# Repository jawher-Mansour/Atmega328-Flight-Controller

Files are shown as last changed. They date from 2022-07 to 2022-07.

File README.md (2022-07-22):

# Atmega328-Flight-Controller
A  Flight Controller board for a quadcopter based on YMFC Joop Brokking's code.

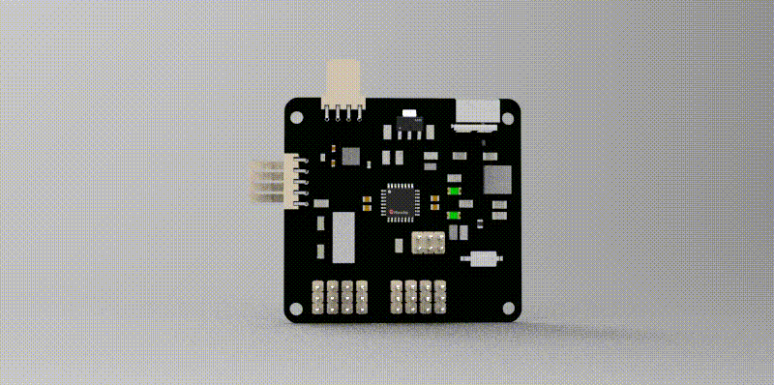
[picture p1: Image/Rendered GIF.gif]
Board Animated GIF
<h1 align="center"></h1>

This is the readme file of the Atmega328-Flight Controller project, which is my contribution to the OPEN SOURCE community. The board was developed by LAB619 Engineering & Consulting Services which is a tech company based in Tunisia that is specialized in custom machine fabrication and embedded solution development, the company is also specialized in developing IoT solutions (LoRa, GPRS, and WiFi), PCB and mechanical design. You can check the website for further information: [LAB619 Engineering & Consulting Services](https://lab619.tn)

This board is an Atmega328 MCU-based flight controller for quadcopters that is easy to build and fun to fly. The board is compatible with Joop BROKKING YMFC-AL (Your Multi-copter Flight Controller -Auto Leveling). Auto leveling means that when you release the sticks the quadcopter levels itself.

## Broadly, this repository consists of:

- Hardware designs (developed using Altium).
- PDF for Schematics
- Bill of Materials Files 
- Footprint Position File 
- Gerber Files 
- Software written using Arduino-IDE
```
📦Atmega328-Flight-Controller
 ┣ 📂Fabrication
 ┃ ┣ 📂Assembly
 ┃ ┗ 📂Gerber
 ┣ 📂Image
 ┣ 📂Altium Files
 ┣ 📂Software
 ┣ 📜.gitignore
 ┣ 📜README.md
 ┣ 📜fabrication and assembly drawings.pdf
 ┗ 📜Schematics.pdf
```
---
## Board Specifications :

The board currently includes:

- MCU: Atmega328 with an I2C, UART, and SPI interfaces.
- IMU: MPU6050 which is a 3-axis gyroscope and a 3-axis accelerometer on the same silicon die with an I2C interface and an interrupt pin.
- 4 PWM outputs to control the motors.
- 4 Timer input channels for the Inputs.
- Batterie voltage measurement system (voltage divider and Zener diode for protection).
- FTDI and ICSP interfaces for programming & debugging.
- LEDs for signaling.

<table>
  <tr>
    <td> 
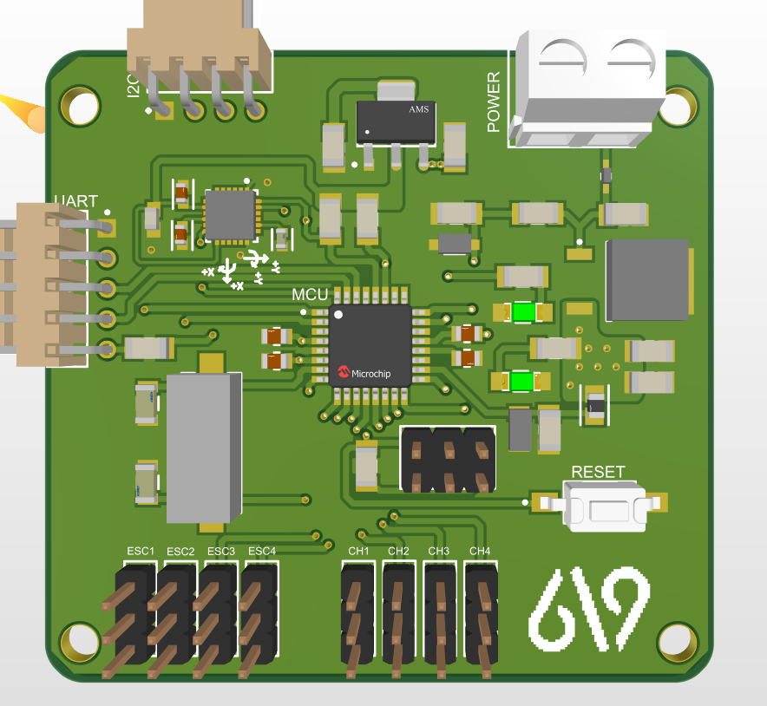
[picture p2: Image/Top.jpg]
PCB Rendred Top View
     
  </td>
  <td>   
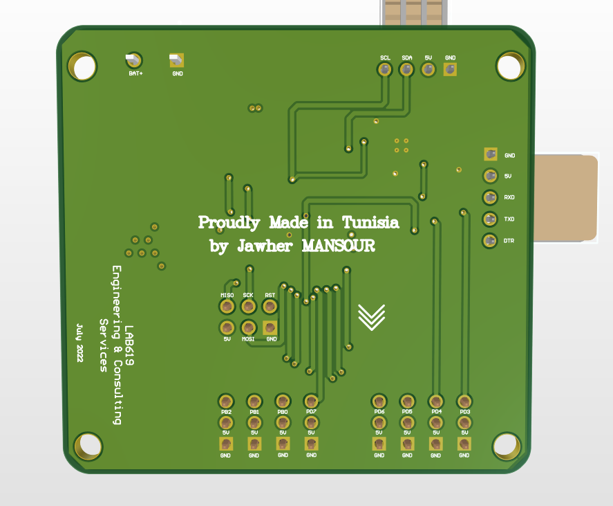
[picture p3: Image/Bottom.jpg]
PCB Rendred Bottom View
    
  </td>  
  </tr> 
  <tr>
    <td> 
      <center> Top side of the PCB </center>
  </td>
  <td> 
      <center>Bottom  side of the PCB</center>
  </td>  
  </tr> 
</table>

## Getting Started:

In order to program the board, it is necessary to use an **AVR ICSP** Programmer. 

If you don't have an AVR ICSP you can use any Arduino board as a programmer as shown in this [link](https://docs.arduino.cc/built-in-examples/arduino-isp/ArduinoISP)

---
### Fabrication

This board can be manufactured and assembled by [JLCPCB](https://jlcpcb.com/). Check the fabrication folder for files related to manufacturing the board

---
### How to setup and program the board 

Use an AVR ICSP programmer or any Arduino board as a programmer to connect to **Atmega328-Flight-Controller**

You need to connect AVR ICSP's 5V,MOSI,MISO,SCK,RESET,GND to Flight Controller board's 5V,MOSI,MISO,SCK,RESET,GND.

Further details can be found on Joop BroKking web page [link](http://www.brokking.net/ymfc-al_main.html) or you can follow this amazing video by Joop [Youtube Video](https://www.youtube.com/watch?v=DYpHB-LfloI&t=1s)

<table>
  <tr>
    <td> 
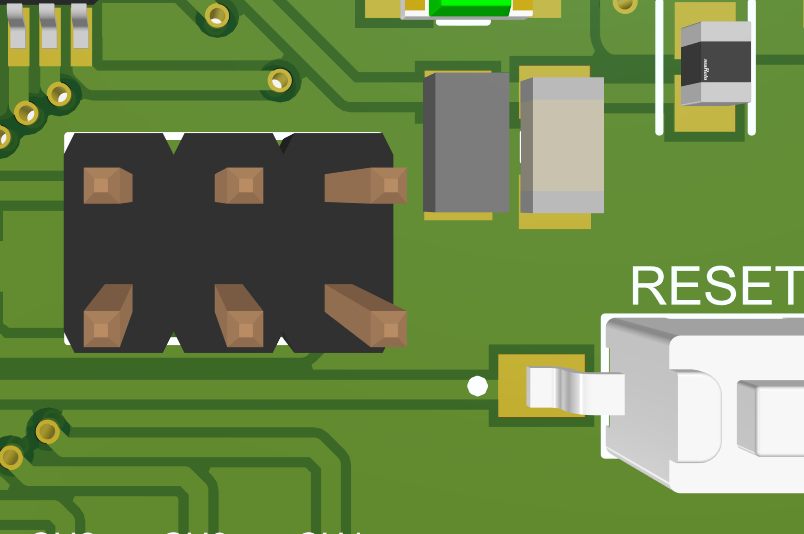
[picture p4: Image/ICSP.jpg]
     
  </td>
  <td>   
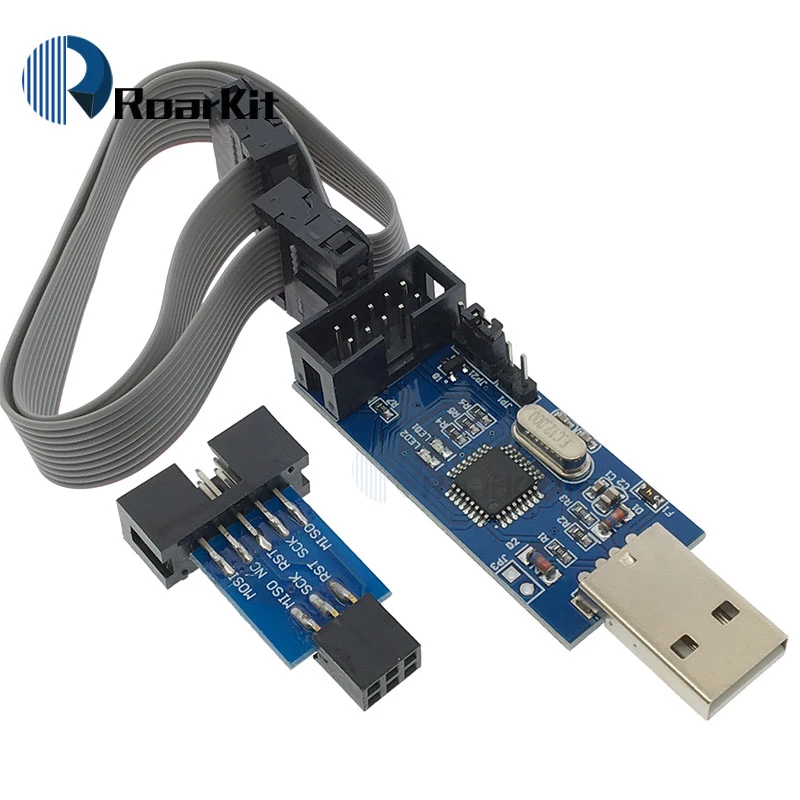
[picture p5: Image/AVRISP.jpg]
   
  </td>  
  </tr> 
  <tr>
    <td> 
    <center>Programming Pins</center>
  </td>
  <td>   
   <center>AVR ICSP programmer</center>
  </td>  
  </tr> 
</table>

---

## Useful ressources
### Datatsheets

- Atmega328 Datasheet [Atmega328](https://ww1.microchip.com/downloads/en/DeviceDoc/Atmel-7810-Automotive-Microcontrollers-ATmega328P_Datasheet.pdf)
- MPU6050 Datasheet [MPU6050](https://invensense.tdk.com/wp-content/uploads/2015/02/MPU-6000-Datasheet1.pdf)

## Credits

- PCB design and hardware engineering : Jawher MANSOUR [Web ](https://jawher-mansour.github.io/) email: jawhermansour@outlook.com

- Software design : Joop Brokking [Web](http://www.brokking.net/)

---

**Note:** ***This repository is reserved for the hardware part of this project, as well as the embedded software of the project.***

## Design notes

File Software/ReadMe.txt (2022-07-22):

Thank you for downloading the YMFC-AL software package. 

Current version: 1.4 April 30, 2017

Content:
YMFC-AL_setup.ino
YMFC-AL_esc_calibrate.ino
YMFC-AL_Flight_controller.ino

Revision update:
=====================================================================================================================================================

Version 1.4 April 30, 2017
The calibration sketch stops working when a character or number is send. When sending a character via the serial monitor of some Arduino IDE’s a line feed is also send. Because the ESC calibration program only expects one character the program stops working.

In the code the line:
data = Serial.read();                                                               //Read the incomming byte.

Is changed into:
data = Serial.read();                                                               //Read the incomming byte.
delay(100);                                                                         //Wait for any other bytes to come in
while(Serial.available() > 0)loop_counter = Serial.read();                          //Empty the Serial buffer.
=====================================================================================================================================================

Version 1.3 October 30, 2016
With the newer Arduino IDE versions (1.6.x and up) the setup program hangs due to optimization of the compiler. This is fixed in this version.

The starting speed of the motors is reduced to 1100us.

=====================================================================================================================================================

Version 1.2 - July 12, 2016
The last code did not fix the complete problem so I had to make another adjustment to the code. The acc_x and acc_y values can also be negative so a simple smaller or greater test does not work.
Therefor I changed the code to:

if(abs(acc_y) < acc_total_vector){                                        //Prevent the asin function to produce a NaN
  angle_pitch_acc = asin((float)acc_y/acc_total_vector)* 57.296;          //Calculate the pitch angle.
}
if(abs(acc_x) < acc_total_vector){                                        //Prevent the asin function to produce a NaN
  angle_roll_acc = asin((float)acc_x/acc_total_vector)* -57.296;          //Calculate the roll angle.
}

This prevents a division by zero and the input value for the asin function will always be smaller than 1.
=====================================================================================================================================================

Version 1.1 - July 11, 2016
There was a NaN (not a number) problem in the code. When flying more aggressive the quadcopter could become uncontrolable. The NaN problem is caused by the following:
When the absolute value of acc_y or acc_x becomes larger that the acc_total_vector the values provided to the asin function is larger than 1 and the asin function produces a NaN.
It recovers when the acc_total_vector becomes larger that the acc_x or acc_y values. But due to the complimentary filter the NaN error persists.
This problem will only occur when flying aggressive / fast descents. 

I changed the code as followed:
from:
angle_pitch_acc = asin((float)acc_y/acc_total_vector)* 57.296;            //Calculate the pitch angle.
angle_roll_acc = asin((float)acc_x/acc_total_vector)* -57.296;            //Calculate the roll angle.

to:
if(acc_y > acc_total_vector){
  angle_pitch_acc = asin((float)acc_y/acc_total_vector)* 57.296;            //Calculate the pitch angle.
}
if(acc_x > acc_total_vector){
  angle_roll_acc = asin((float)acc_x/acc_total_vector)* -57.296;            //Calculate the roll angle.
}
=====================================================================================================================================================

Version 1.0 - July 3, 2016
Release
=====================================================================================================================================================

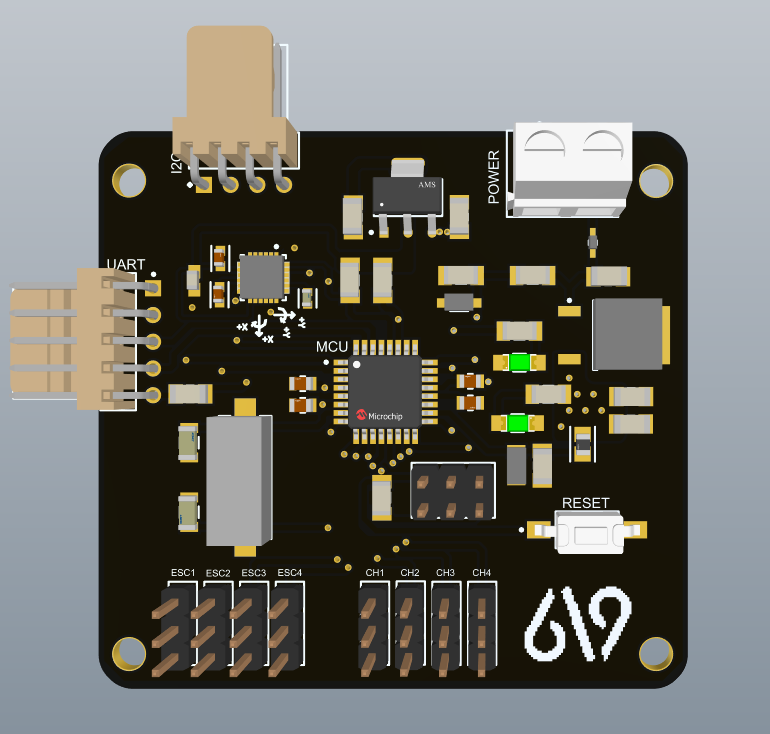
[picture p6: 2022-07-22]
Image/CapturePCB.jpg

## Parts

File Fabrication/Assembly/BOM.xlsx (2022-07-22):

Comment | Designator | Footprint
1uF | C1 | C1206
100nF | C2, C15, C16 | CAPC3216X95X55NL15T25
100nF | C3, C9, C12, C13 | FP-GRM21B-0_15-MFG
100nF | C4, C7 | C0603
10nF | C5 | C0603
2nF2 | C6 | C0603
22pF | C8, C10 | C1206
4.7uF | C11 | CAPC3216X95X55NL15T25
330nF | C14 | CAPC3216X95X55NL15T25
10uF | C17, C18 | CAPC3216X95X55NL15T25
1N4148WT | D1 | FAIR-SOD-523F-2_V
MMSZ5230B-E3-08 | D2 | VISH-SOD-123-2_V
HSMG-C150 | D3, D4 | FP-HSMG-C150-MFG
100MHz | FB1 | FP-BLM21-0_2-t0_85-e0_5-IPC_A
2K2 | R1, R2 | R1206
10K | R3, R4 | R1206
1K | R5 | R1206
330 | R6, R7 | R1206
FSMSM | SW1 | TECO-FSMSM-2_V
ATmega328P-AU | U1 | FP-32A-MFG
MPU-6050 | U2 | IS-QFN-24_V
L7805CDT-TR | U3 | TO-252_N
AMS1117-3.3 | U4 | FP-AMS1117-IPC_C
16MHz | X1 | FOX-FOXSDLF160-20_V

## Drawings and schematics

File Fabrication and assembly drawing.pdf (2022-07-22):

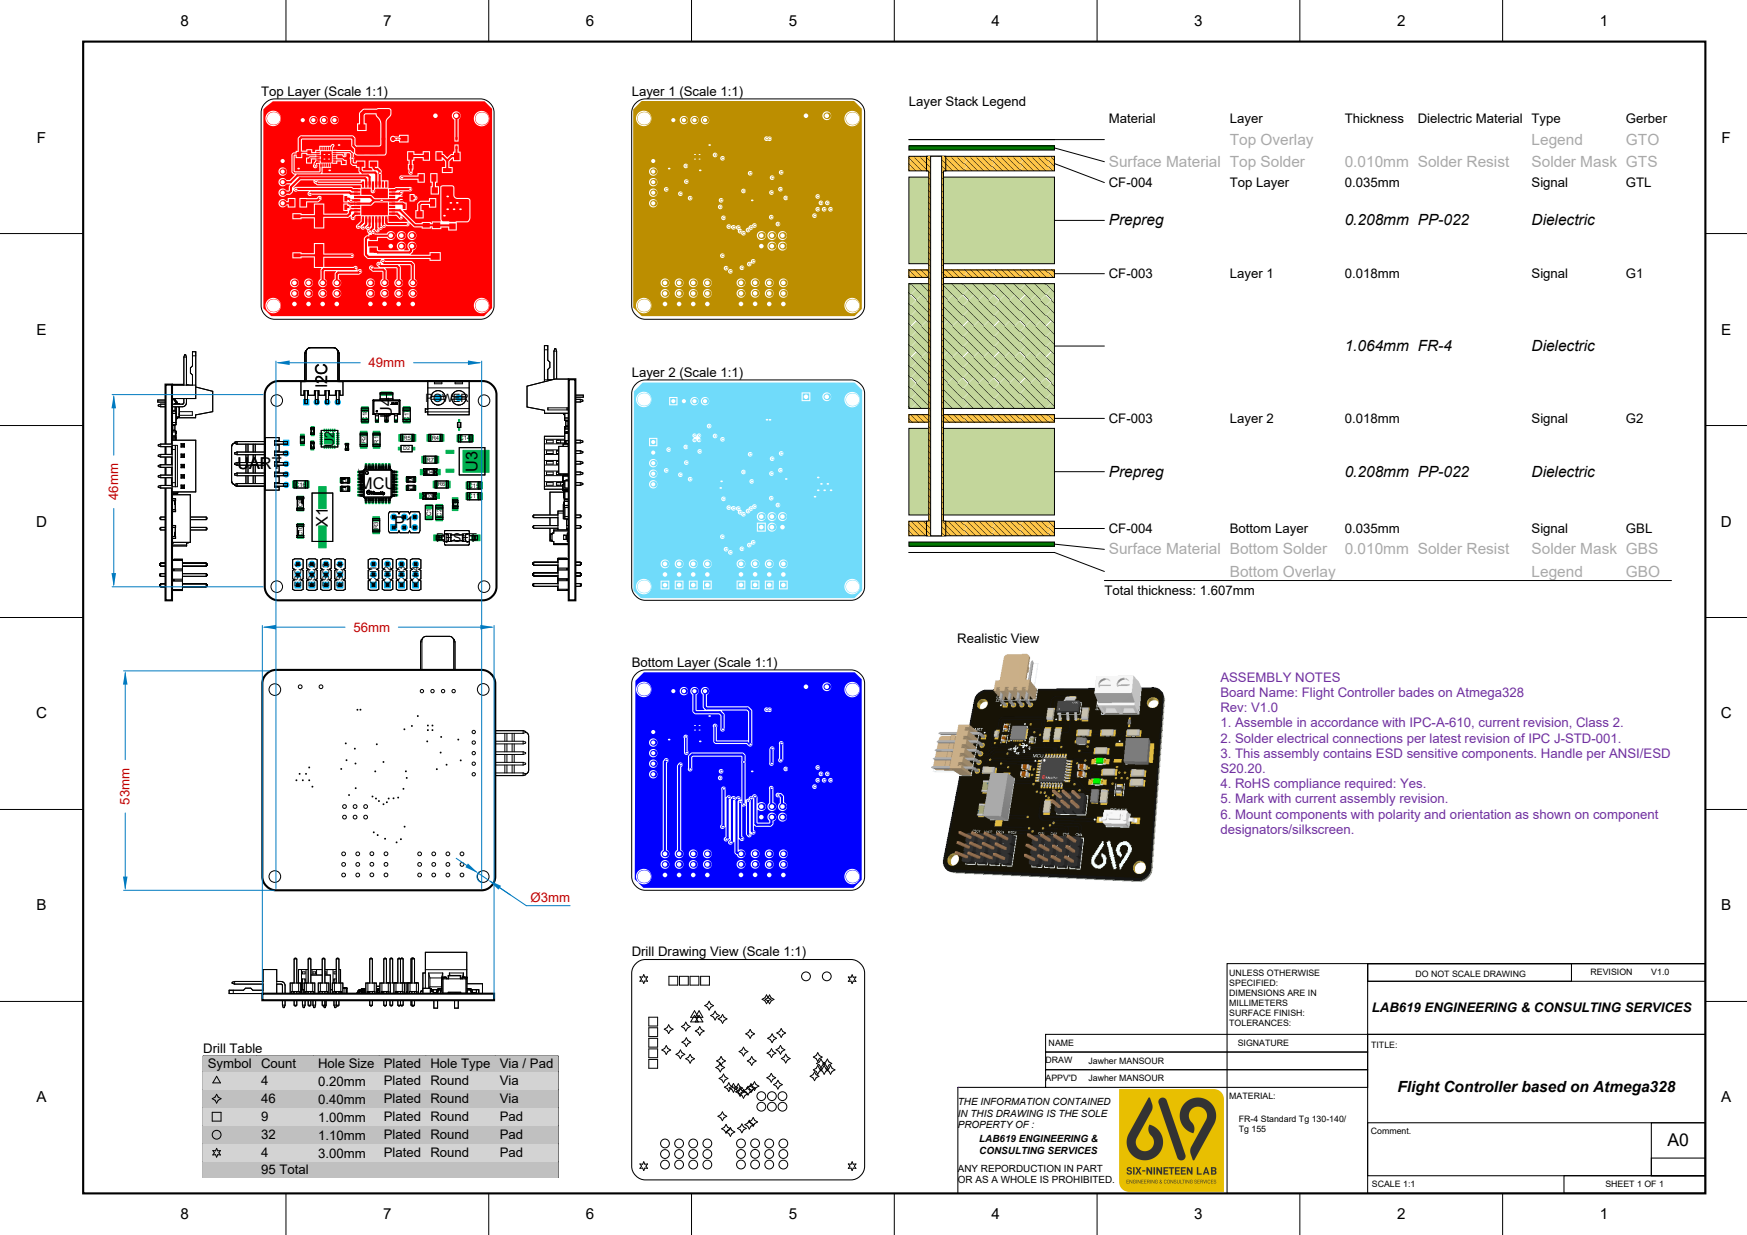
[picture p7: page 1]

ASSEMBLY NOTES
Board Name: Flight Controller bades on Atmega328
Rev: V1.0
1. Assemble in accordance with IPC-A-610, current revision, Class 2.
2. Solder electrical connections per latest revision of IPC J-STD-001.
3. This assembly contains ESD sensitive components. Handle per ANSI/ESD
4. RoHS compliance required: Yes.
5. Mark with current assembly revision.
6. Mount components with polarity and orientation as shown on component
designators/silkscreen.

Drill Drawing View (Scale 1:1)

Flight Controller based on Atmega328

THE INFORMATION CONTAINED
IN THIS DRAWING IS THE SOLE
PROPERTY OF :
LAB619 ENGINEERING &
CONSULTING SERVICES
ANY REPORDUCTION IN PART
OR AS A WHOLE IS PROHIBITED.

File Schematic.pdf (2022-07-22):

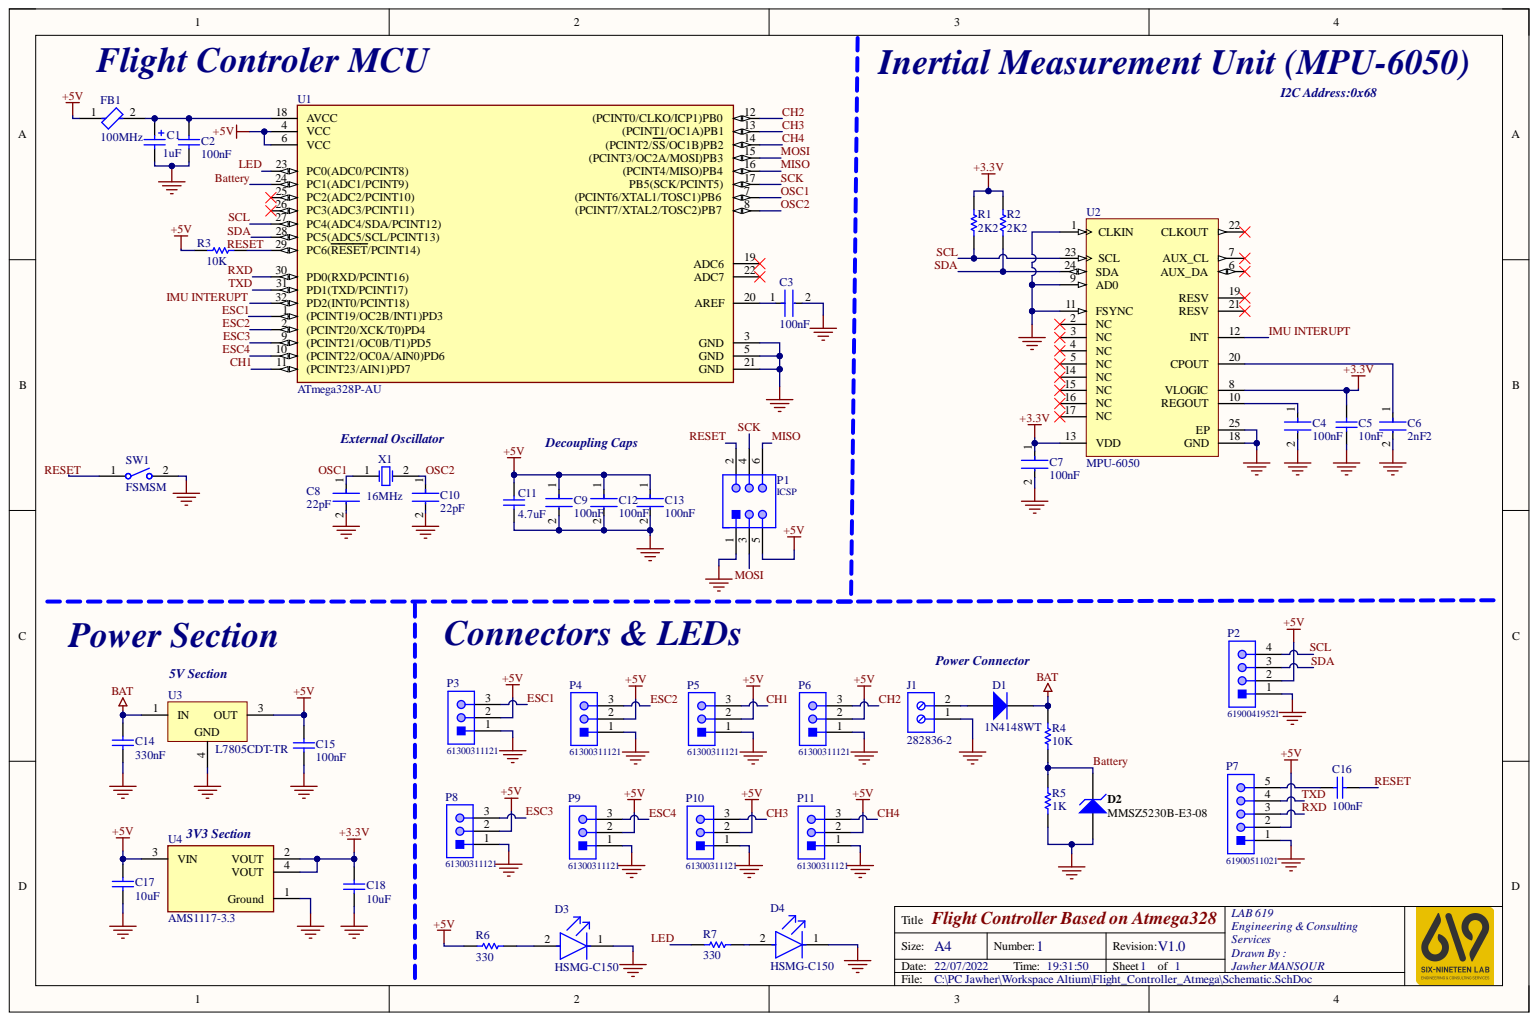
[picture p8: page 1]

Inertial Measurement Unit (MPU-6050)

VCC 4
VCC 6

SCL 23

Flight Controller Based on Atmega328
Title

Size: A4 | Number: 1 | Revision: V1.0
Date: 22/07/2022 Time: 19:31:50 | | Sheet 1 of

C:\PC Jawher\Workspace Altium\Flight_Controller_Atmega\Schematic.SchDoc

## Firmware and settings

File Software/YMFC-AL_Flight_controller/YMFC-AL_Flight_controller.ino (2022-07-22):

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
#include <Wire.h>                          //Include the Wire.h library so we can communicate with the gyro.
#include <EEPROM.h>                        //Include the EEPROM.h library so we can store information onto the EEPROM

///////////////////////////////////////////////////////////////////////////////////////////////////////////////////////////////////////
//PID gain and limit settings
///////////////////////////////////////////////////////////////////////////////////////////////////////////////////////////////////////
float pid_p_gain_roll = 1.3;               //Gain setting for the roll P-controller
float pid_i_gain_roll = 0.04;              //Gain setting for the roll I-controller
float pid_d_gain_roll = 18.0;              //Gain setting for the roll D-controller
int pid_max_roll = 400;                    //Maximum output of the PID-controller (+/-)

float pid_p_gain_pitch = pid_p_gain_roll;  //Gain setting for the pitch P-controller.
float pid_i_gain_pitch = pid_i_gain_roll;  //Gain setting for the pitch I-controller.
float pid_d_gain_pitch = pid_d_gain_roll;  //Gain setting for the pitch D-controller.
int pid_max_pitch = pid_max_roll;          //Maximum output of the PID-controller (+/-)

float pid_p_gain_yaw = 4.0;                //Gain setting for the pitch P-controller. //4.0
float pid_i_gain_yaw = 0.02;               //Gain setting for the pitch I-controller. //0.02
float pid_d_gain_yaw = 0.0;                //Gain setting for the pitch D-controller.
int pid_max_yaw = 400;                     //Maximum output of the PID-controller (+/-)

boolean auto_level = true;                 //Auto level on (true) or off (false)

///////////////////////////////////////////////////////////////////////////////////////////////////////////////////////////////////////
//Declaring global variables
///////////////////////////////////////////////////////////////////////////////////////////////////////////////////////////////////////
byte last_channel_1, last_channel_2, last_channel_3, last_channel_4;
byte eeprom_data[36];
byte highByte, lowByte;
volatile int receiver_input_channel_1, receiver_input_channel_2, receiver_input_channel_3, receiver_input_channel_4;
int counter_channel_1, counter_channel_2, counter_channel_3, counter_channel_4, loop_counter;
int esc_1, esc_2, esc_3, esc_4;
int throttle, battery_voltage;
int cal_int, start, gyro_address;
int receiver_input[5];
int temperature;
int acc_axis[4], gyro_axis[4];
float roll_level_adjust, pitch_level_adjust;

long acc_x, acc_y, acc_z, acc_total_vector;
unsigned long timer_channel_1, timer_channel_2, timer_channel_3, timer_channel_4, esc_timer, esc_loop_timer;
unsigned long timer_1, timer_2, timer_3, timer_4, current_time;
unsigned long loop_timer;
double gyro_pitch, gyro_roll, gyro_yaw;
double gyro_axis_cal[4];
float pid_error_temp;
float pid_i_mem_roll, pid_roll_setpoint, gyro_roll_input, pid_output_roll, pid_last_roll_d_error;
float pid_i_mem_pitch, pid_pitch_setpoint, gyro_pitch_input, pid_output_pitch, pid_last_pitch_d_error;
float pid_i_mem_yaw, pid_yaw_setpoint, gyro_yaw_input, pid_output_yaw, pid_last_yaw_d_error;
float angle_roll_acc, angle_pitch_acc, angle_pitch, angle_roll;
boolean gyro_angles_set;

///////////////////////////////////////////////////////////////////////////////////////////////////////////////////////////////////////
//Setup routine
///////////////////////////////////////////////////////////////////////////////////////////////////////////////////////////////////////
void setup(){
  //Serial.begin(57600);
  //Copy the EEPROM data for fast access data.
  for(start = 0; start <= 35; start++)eeprom_data[start] = EEPROM.read(start);
  start = 0;                                                                //Set start back to zero.
  gyro_address = eeprom_data[32];                                           //Store the gyro address in the variable.

  Wire.begin();                                                             //Start the I2C as master.

  TWBR = 12;                                                                //Set the I2C clock speed to 400kHz.

  //Arduino (Atmega) pins default to inputs, so they don't need to be explicitly declared as inputs.
  DDRD |= B11110000;                                                        //Configure digital poort 4, 5, 6 and 7 as output.
  DDRB |= B00110000;                                                        //Configure digital poort 12 and 13 as output.

  //Use the led on the Arduino for startup indication.
  digitalWrite(12,HIGH);                                                    //Turn on the warning led.

  //Check the EEPROM signature to make sure that the setup program is executed.
  while(eeprom_data[33] != 'J' || eeprom_data[34] != 'M' || eeprom_data[35] != 'B')delay(10);

  //The flight controller needs the MPU-6050 with gyro and accelerometer
  //If setup is completed without MPU-6050 stop the flight controller program  
  if(eeprom_data[31] == 2 || eeprom_data[31] == 3)delay(10);

  set_gyro_registers();                                                     //Set the specific gyro registers.

  for (cal_int = 0; cal_int < 1250 ; cal_int ++){                           //Wait 5 seconds before continuing.
    PORTD |= B11110000;                                                     //Set digital poort 4, 5, 6 and 7 high.
    delayMicroseconds(1000);                                                //Wait 1000us.
    PORTD &= B00001111;                                                     //Set digital poort 4, 5, 6 and 7 low.
    delayMicroseconds(3000);                                                //Wait 3000us.
  }

  //Let's take multiple gyro data samples so we can determine the average gyro offset (calibration).
  for (cal_int = 0; cal_int < 2000 ; cal_int ++){                           //Take 2000 readings for calibration.
    if(cal_int % 15 == 0)digitalWrite(12, !digitalRead(12));                //Change the led status to indicate calibration.
    gyro_signalen();                                                        //Read the gyro output.
    gyro_axis_cal[1] += gyro_axis[1];                                       //Ad roll value to gyro_roll_cal.
    gyro_axis_cal[2] += gyro_axis[2];                                       //Ad pitch value to gyro_pitch_cal.
    gyro_axis_cal[3] += gyro_axis[3];                                       //Ad yaw value to gyro_yaw_cal.
    //We don't want the esc's to be beeping annoyingly. So let's give them a 1000us puls while calibrating the gyro.
    PORTD |= B11110000;                                                     //Set digital poort 4, 5, 6 and 7 high.
    delayMicroseconds(1000);                                                //Wait 1000us.
    PORTD &= B00001111;                                                     //Set digital poort 4, 5, 6 and 7 low.
    delay(3);                                                               //Wait 3 milliseconds before the next loop.
  }
  //Now that we have 2000 measures, we need to devide by 2000 to get the average gyro offset.
  gyro_axis_cal[1] /= 2000;                                                 //Divide the roll total by 2000.
  gyro_axis_cal[2] /= 2000;                                                 //Divide the pitch total by 2000.
  gyro_axis_cal[3] /= 2000;                                                 //Divide the yaw total by 2000.

  PCICR |= (1 << PCIE0);                                                    //Set PCIE0 to enable PCMSK0 scan.
  PCMSK0 |= (1 << PCINT0);                                                  //Set PCINT0 (digital input 8) to trigger an interrupt on state change.
  PCMSK0 |= (1 << PCINT1);                                                  //Set PCINT1 (digital input 9)to trigger an interrupt on state change.
  PCMSK0 |= (1 << PCINT2);                                                  //Set PCINT2 (digital input 10)to trigger an interrupt on state change.
  PCMSK0 |= (1 << PCINT3);                                                  //Set PCINT3 (digital input 11)to trigger an interrupt on state change.

  //Wait until the receiver is active and the throtle is set to the lower position.
  while(receiver_input_channel_3 < 990 || receiver_input_channel_3 > 1020 || receiver_input_channel_4 < 1400){
    receiver_input_channel_3 = convert_receiver_channel(3);                 //Convert the actual receiver signals for throttle to the standard 1000 - 2000us
    receiver_input_channel_4 = convert_receiver_channel(4);                 //Convert the actual receiver signals for yaw to the standard 1000 - 2000us
    start ++;                                                               //While waiting increment start whith every loop.
    //We don't want the esc's to be beeping annoyingly. So let's give them a 1000us puls while waiting for the receiver inputs.
    PORTD |= B11110000;                                                     //Set digital poort 4, 5, 6 and 7 high.
    delayMicroseconds(1000);                                                //Wait 1000us.
    PORTD &= B00001111;                                                     //Set digital poort 4, 5, 6 and 7 low.
    delay(3);                                                               //Wait 3 milliseconds before the next loop.
    if(start == 125){                                                       //Every 125 loops (500ms).
      digitalWrite(12, !digitalRead(12));                                   //Change the led status.
      start = 0;                                                            //Start again at 0.
    }
  }
  start = 0;                                                                //Set start back to 0.

  //Load the battery voltage to the battery_voltage variable.
  //65 is the voltage compensation for the diode.
  //12.6V equals ~5V @ Analog 0.
  //12.6V equals 1023 analogRead(0).
  //1260 / 1023 = 1.2317.
  //The variable battery_voltage holds 1050 if the battery voltage is 10.5V.
  battery_voltage = (analogRead(0) + 65) * 1.2317;

  loop_timer = micros();                                                    //Set the timer for the next loop.

  //When everything is done, turn off the led.
  digitalWrite(12,LOW);                                                     //Turn off the warning led.
}
///////////////////////////////////////////////////////////////////////////////////////////////////////////////////////////////////////
//Main program loop
///////////////////////////////////////////////////////////////////////////////////////////////////////////////////////////////////////
void loop(){

  //65.5 = 1 deg/sec (check the datasheet of the MPU-6050 for more information).
  gyro_roll_input = (gyro_roll_input * 0.7) + ((gyro_roll / 65.5) * 0.3);   //Gyro pid input is deg/sec.
  gyro_pitch_input = (gyro_pitch_input * 0.7) + ((gyro_pitch / 65.5) * 0.3);//Gyro pid input is deg/sec.
  gyro_yaw_input = (gyro_yaw_input * 0.7) + ((gyro_yaw / 65.5) * 0.3);      //Gyro pid input is deg/sec.


  ////////////////////////////////////////////////////////////////////////////////////////////////////
  //This is the added IMU code from the videos:
  //https://youtu.be/4BoIE8YQwM8
  //https://youtu.be/j-kE0AMEWy4
  ////////////////////////////////////////////////////////////////////////////////////////////////////
  
  //Gyro angle calculations
  //0.0000611 = 1 / (250Hz / 65.5)
  angle_pitch += gyro_pitch * 0.0000611;                                    //Calculate the traveled pitch angle and add this to the angle_pitch variable.
  angle_roll += gyro_roll * 0.0000611;                                      //Calculate the traveled roll angle and add this to the angle_roll variable.

  //0.000001066 = 0.0000611 * (3.142(PI) / 180degr) The Arduino sin function is in radians
  angle_pitch -= angle_roll * sin(gyro_yaw * 0.000001066);                  //If the IMU has yawed transfer the roll angle to the pitch angel.
  angle_roll += angle_pitch * sin(gyro_yaw * 0.000001066);                  //If the IMU has yawed transfer the pitch angle to the roll angel.

  //Accelerometer angle calculations
  acc_total_vector = sqrt((acc_x*acc_x)+(acc_y*acc_y)+(acc_z*acc_z));       //Calculate the total accelerometer vector.
  
  if(abs(acc_y) < acc_total_vector){                                        //Prevent the asin function to produce a NaN
    angle_pitch_acc = asin((float)acc_y/acc_total_vector)* 57.296;          //Calculate the pitch angle.
  }
  if(abs(acc_x) < acc_total_vector){                                        //Prevent the asin function to produce a NaN
    angle_roll_acc = asin((float)acc_x/acc_total_vector)* -57.296;          //Calculate the roll angle.
  }
  
  //Place the MPU-6050 spirit level and note the values in the following two lines for calibration.
  angle_pitch_acc -= 0.0;                                                   //Accelerometer calibration value for pitch.
  angle_roll_acc -= 0.0;                                                    //Accelerometer calibration value for roll.
  
  angle_pitch = angle_pitch * 0.9996 + angle_pitch_acc * 0.0004;            //Correct the drift of the gyro pitch angle with the accelerometer pitch angle.
  angle_roll = angle_roll * 0.9996 + angle_roll_acc * 0.0004;               //Correct the drift of the gyro roll angle with the accelerometer roll angle.

  pitch_level_adjust = angle_pitch * 15;                                    //Calculate the pitch angle correction
  roll_level_adjust = angle_roll * 15;                                      //Calculate the roll angle correction

  if(!auto_level){                                                          //If the quadcopter is not in auto-level mode
    pitch_level_adjust = 0;                                                 //Set the pitch angle correction to zero.
    roll_level_adjust = 0;                                                  //Set the roll angle correcion to zero.
  }


  //For starting the motors: throttle low and yaw left (step 1).
  if(receiver_input_channel_3 < 1050 && receiver_input_channel_4 < 1050)start = 1;
  //When yaw stick is back in the center position start the motors (step 2).
  if(start == 1 && receiver_input_channel_3 < 1050 && receiver_input_channel_4 > 1450){
    start = 2;

    angle_pitch = angle_pitch_acc;                                          //Set the gyro pitch angle equal to the accelerometer pitch angle when the quadcopter is started.
    angle_roll = angle_roll_acc;                                            //Set the gyro roll angle equal to the accelerometer roll angle when the quadcopter is started.
    gyro_angles_set = true;                                                 //Set the IMU started flag.

    //Reset the PID controllers for a bumpless start.
    pid_i_mem_roll = 0;
    pid_last_roll_d_error = 0;
    pid_i_mem_pitch = 0;
    pid_last_pitch_d_error = 0;
    pid_i_mem_yaw = 0;
    pid_last_yaw_d_error = 0;
  }
  //Stopping the motors: throttle low and yaw right.
  if(start == 2 && receiver_input_channel_3 < 1050 && receiver_input_channel_4 > 1950)start = 0;

  //The PID set point in degrees per second is determined by the roll receiver input.
  //In the case of deviding by 3 the max roll rate is aprox 164 degrees per second ( (500-8)/3 = 164d/s ).
  pid_roll_setpoint = 0;
  //We need a little dead band of 16us for better results.
  if(receiver_input_channel_1 > 1508)pid_roll_setpoint = receiver_input_channel_1 - 1508;
  else if(receiver_input_channel_1 < 1492)pid_roll_setpoint = receiver_input_channel_1 - 1492;

  pid_roll_setpoint -= roll_level_adjust;                                   //Subtract the angle correction from the standardized receiver roll input value.
  pid_roll_setpoint /= 3.0;                                                 //Divide the setpoint for the PID roll controller by 3 to get angles in degrees.


  //The PID set point in degrees per second is determined by the pitch receiver input.
  //In the case of deviding by 3 the max pitch rate is aprox 164 degrees per second ( (500-8)/3 = 164d/s ).
  pid_pitch_setpoint = 0;
  //We need a little dead band of 16us for better results.
  if(receiver_input_channel_2 > 1508)pid_pitch_setpoint = receiver_input_channel_2 - 1508;
  else if(receiver_input_channel_2 < 1492)pid_pitch_setpoint = receiver_input_channel_2 - 1492;

  pid_pitch_setpoint -= pitch_level_adjust;                                  //Subtract the angle correction from the standardized receiver pitch input value.
  pid_pitch_setpoint /= 3.0;                                                 //Divide the setpoint for the PID pitch controller by 3 to get angles in degrees.

  //The PID set point in degrees per second is determined by the yaw receiver input.
  //In the case of deviding by 3 the max yaw rate is aprox 164 degrees per second ( (500-8)/3 = 164d/s ).
  pid_yaw_setpoint = 0;
  //We need a little dead band of 16us for better results.
  if(receiver_input_channel_3 > 1050){ //Do not yaw when turning off the motors.
    if(receiver_input_channel_4 > 1508)pid_yaw_setpoint = (receiver_input_channel_4 - 1508)/3.0;
    else if(receiver_input_channel_4 < 1492)pid_yaw_setpoint = (receiver_input_channel_4 - 1492)/3.0;
  }
  
  calculate_pid();                                                            //PID inputs are known. So we can calculate the pid output.

  //The battery voltage is needed for compensation.
  //A complementary filter is used to reduce noise.
  //0.09853 = 0.08 * 1.2317.
  battery_voltage = battery_voltage * 0.92 + (analogRead(0) + 65) * 0.09853;

  //Turn on the led if battery voltage is to low.
  if(battery_voltage < 1000 && battery_voltage > 600)digitalWrite(12, HIGH);


  throttle = receiver_input_channel_3;                                      //We need the throttle signal as a base signal.

  if (start == 2){                                                          //The motors are started.
    if (throttle > 1800) throttle = 1800;                                   //We need some room to keep full control at full throttle.
    esc_1 = throttle - pid_output_pitch + pid_output_roll - pid_output_yaw; //Calculate the pulse for esc 1 (front-right - CCW)
    esc_2 = throttle + pid_output_pitch + pid_output_roll + pid_output_yaw; //Calculate the pulse for esc 2 (rear-right - CW)
    esc_3 = throttle + pid_output_pitch - pid_output_roll - pid_output_yaw; //Calculate the pulse for esc 3 (rear-left - CCW)
    esc_4 = throttle - pid_output_pitch - pid_output_roll + pid_output_yaw; //Calculate the pulse for esc 4 (front-left - CW)

    if (battery_voltage < 1240 && battery_voltage > 800){                   //Is the battery connected?
      esc_1 += esc_1 * ((1240 - battery_voltage)/(float)3500);              //Compensate the esc-1 pulse for voltage drop.
      esc_2 += esc_2 * ((1240 - battery_voltage)/(float)3500);              //Compensate the esc-2 pulse for voltage drop.
      esc_3 += esc_3 * ((1240 - battery_voltage)/(float)3500);              //Compensate the esc-3 pulse for voltage drop.
      esc_4 += esc_4 * ((1240 - battery_voltage)/(float)3500);              //Compensate the esc-4 pulse for voltage drop.
    } 

    if (esc_1 < 1100) esc_1 = 1100;                                         //Keep the motors running.
    if (esc_2 < 1100) esc_2 = 1100;                                         //Keep the motors running.
    if (esc_3 < 1100) esc_3 = 1100;                                         //Keep the motors running.
    if (esc_4 < 1100) esc_4 = 1100;                                         //Keep the motors running.

    if(esc_1 > 2000)esc_1 = 2000;                                           //Limit the esc-1 pulse to 2000us.
    if(esc_2 > 2000)esc_2 = 2000;                                           //Limit the esc-2 pulse to 2000us.
    if(esc_3 > 2000)esc_3 = 2000;                                           //Limit the esc-3 pulse to 2000us.
    if(esc_4 > 2000)esc_4 = 2000;                                           //Limit the esc-4 pulse to 2000us.  
  }

  else{
    esc_1 = 1000;                                                           //If start is not 2 keep a 1000us pulse for ess-1.
    esc_2 = 1000;                                                           //If start is not 2 keep a 1000us pulse for ess-2.
    esc_3 = 1000;                                                           //If start is not 2 keep a 1000us pulse for ess-3.
    esc_4 = 1000;                                                           //If start is not 2 keep a 1000us pulse for ess-4.
  }

  ////////////////////////////////////////////////////////////////////////////////////////////////////
  //Creating the pulses for the ESC's is explained in this video:
  //https://youtu.be/fqEkVcqxtU8
  ////////////////////////////////////////////////////////////////////////////////////////////////////

  //! ! ! ! ! ! ! ! ! ! ! ! ! ! ! ! ! ! ! ! ! ! ! ! ! ! ! ! ! ! ! ! ! ! ! ! ! ! ! ! ! ! ! ! ! ! ! ! ! !
  //Because of the angle calculation the loop time is getting very important. If the loop time is 
  //longer or shorter than 4000us the angle calculation is off. If you modify the code make sure 
  //that the loop time is still 4000us and no longer! More information can be found on 
  //the Q&A page: 
  //! ! ! ! ! ! ! ! ! ! ! ! ! ! ! ! ! ! ! ! ! ! ! ! ! ! ! ! ! ! ! ! ! ! ! ! ! ! ! ! ! ! ! ! ! ! ! ! ! !
    
  if(micros() - loop_timer > 4050)digitalWrite(12, HIGH);                   //Turn on the LED if the loop time exceeds 4050us.
  
  //All the information for controlling the motor's is available.
  //The refresh rate is 250Hz. That means the esc's need there pulse every 4ms.
  while(micros() - loop_timer < 4000);                                      //We wait until 4000us are passed.
  loop_timer = micros();                                                    //Set the timer for the next loop.
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
